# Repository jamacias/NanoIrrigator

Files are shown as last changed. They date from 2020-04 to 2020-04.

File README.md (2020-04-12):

# NanoIrrigator
A small Arduino Nano PCB shield for controlling solenoid valves for irrigation systems.

The current design is for a single channel, but may be expanded to more channels if there exists more space.

## Main features
* Single-sided PCB for CNC milling.
* 24VAC solenoid valve control with TRIAC and opto-isolator.
* Snubber circuit.

## Pics
<p align="center">
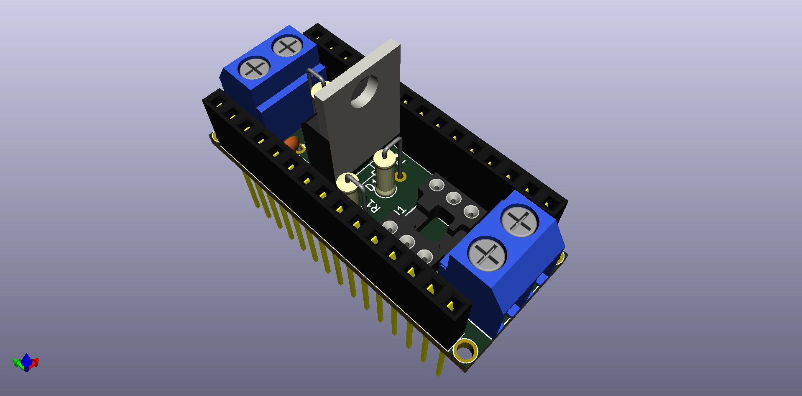
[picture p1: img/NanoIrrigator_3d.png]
    
</p>
<p align="center">
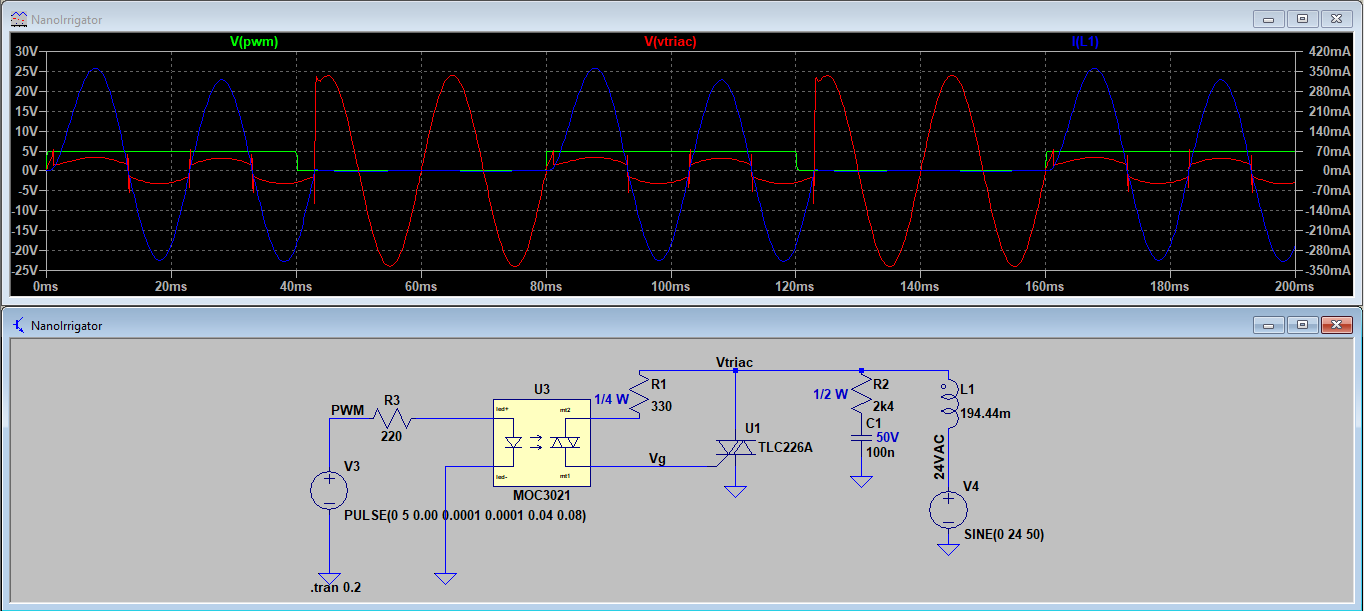
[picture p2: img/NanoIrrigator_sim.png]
    
</p>
<p align="center">
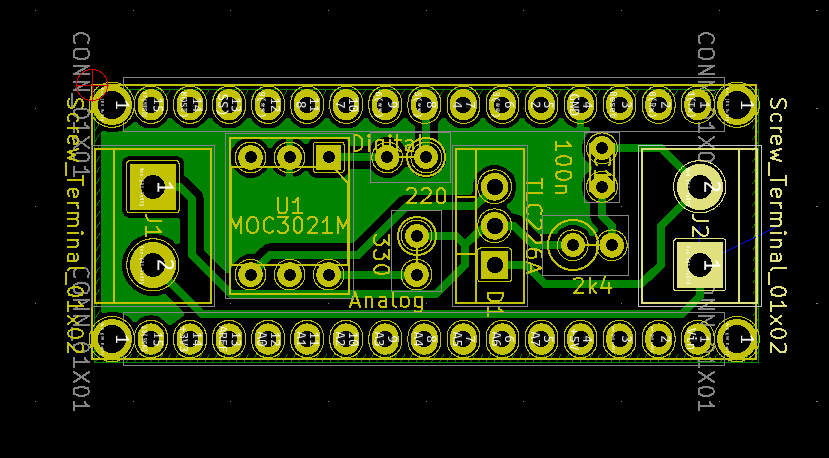
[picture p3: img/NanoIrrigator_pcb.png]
    
</p>

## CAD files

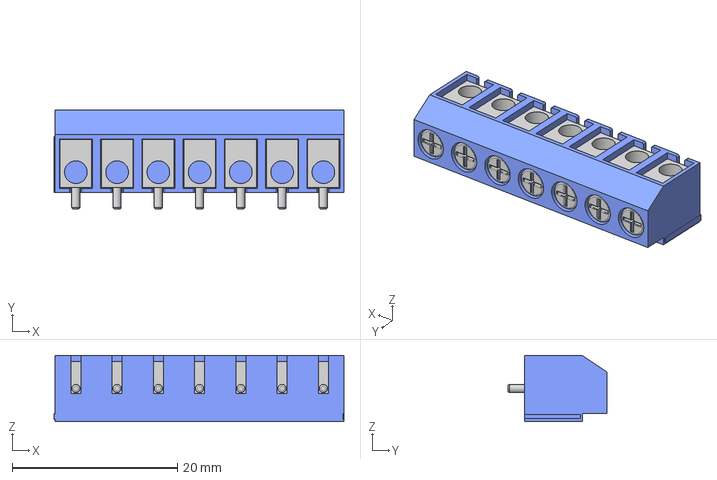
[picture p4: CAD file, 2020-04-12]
NanoIrrigator/3d_models/screw-terminal-block-5mm-2.snapshot.17/Screw Terminal Block 5mm Blue 7-way.step
35.1 x 12.0 x 8.00 mm

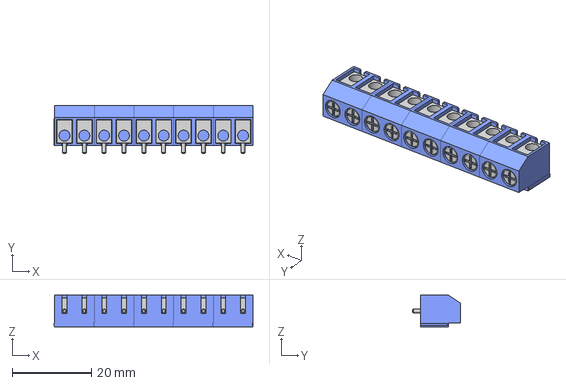
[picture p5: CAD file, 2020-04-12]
NanoIrrigator/3d_models/screw-terminal-block-5mm-2.snapshot.17/Screw Terminal Block 5mm Blue 10-way.stp
50.1 x 12.0 x 8.00 mm
Screw Terminal Block 5mm Blue 2-way x 5

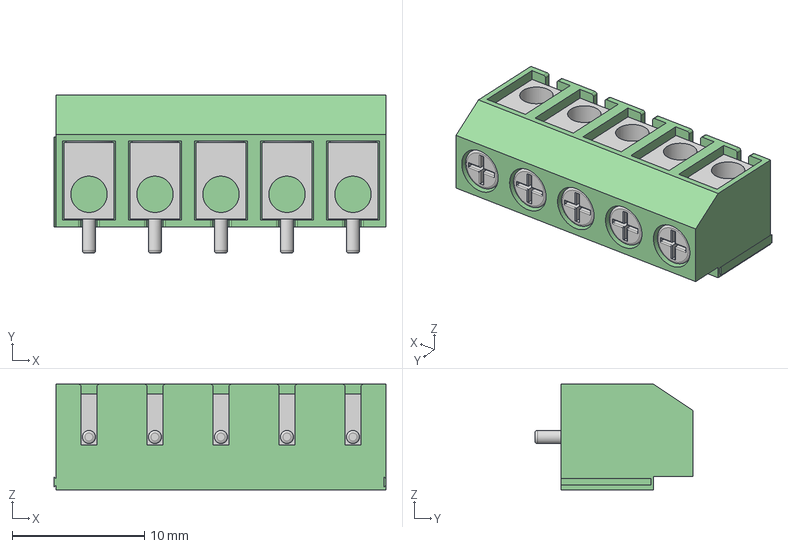
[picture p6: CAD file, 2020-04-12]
NanoIrrigator/3d_models/screw-terminal-block-5mm-2.snapshot.17/Screw Terminal Block 5mm 5-way.step
25.1 x 12.0 x 8.00 mm

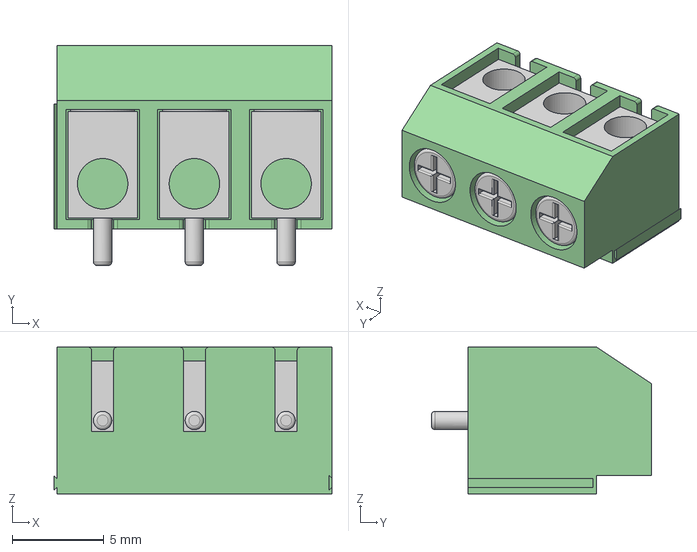
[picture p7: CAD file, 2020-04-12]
NanoIrrigator/3d_models/screw-terminal-block-5mm-2.snapshot.17/Screw Terminal Block 5mm 3-way.step
15.2 x 12.0 x 8.00 mm

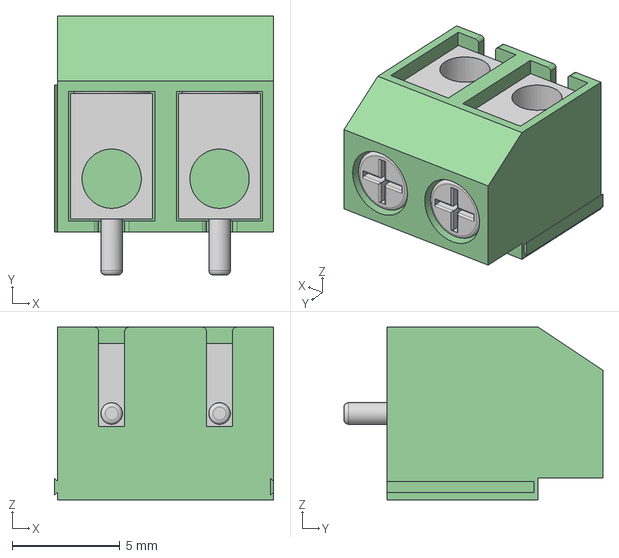
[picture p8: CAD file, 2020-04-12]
NanoIrrigator/3d_models/screw-terminal-block-5mm-2.snapshot.17/Screw Terminal Block 5mm 2-way.step
10.2 x 12.0 x 8.00 mm

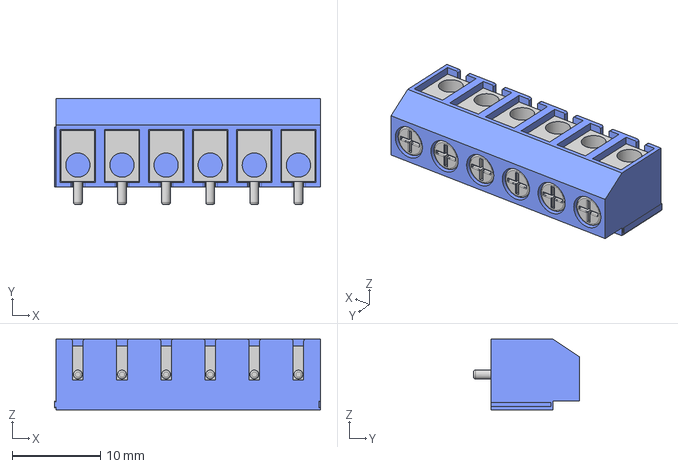
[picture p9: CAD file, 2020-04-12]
NanoIrrigator/3d_models/screw-terminal-block-5mm-2.snapshot.17/Screw Terminal Block 5mm Blue 6-way.step
30.1 x 12.0 x 8.00 mm

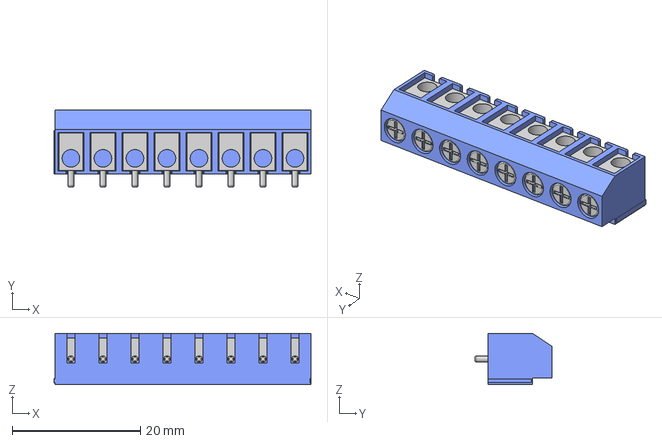
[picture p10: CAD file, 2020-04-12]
NanoIrrigator/3d_models/screw-terminal-block-5mm-2.snapshot.17/Screw Terminal Block 5mm Blue 8-way.step
40.1 x 12.0 x 8.00 mm

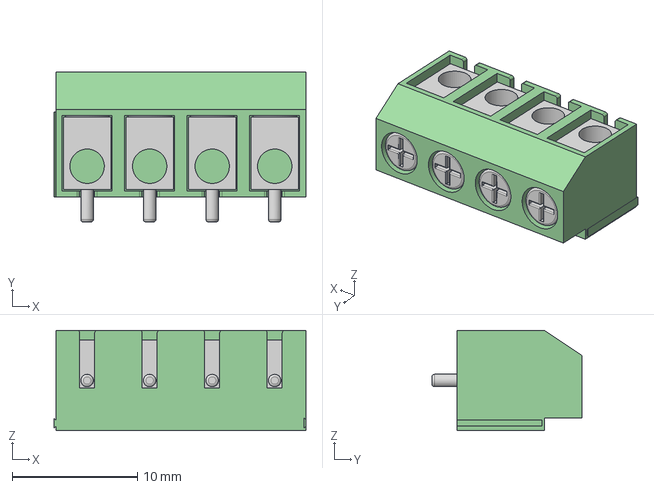
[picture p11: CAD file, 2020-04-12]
NanoIrrigator/3d_models/screw-terminal-block-5mm-2.snapshot.17/Screw Terminal Block 5mm 4-way.step
20.1 x 12.0 x 8.00 mm

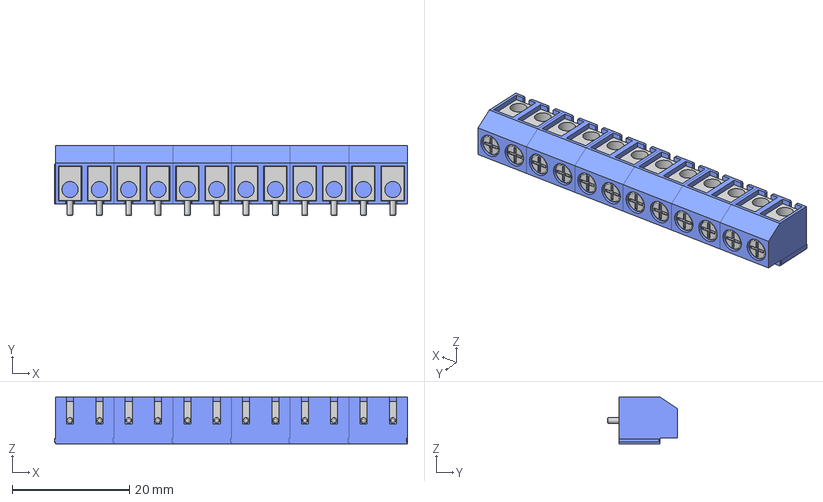
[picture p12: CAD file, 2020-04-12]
NanoIrrigator/3d_models/screw-terminal-block-5mm-2.snapshot.17/Screw Terminal Block 5mm Blue 12-way.stp
60.1 x 12.0 x 8.00 mm
Screw Terminal Block 5mm Blue 2-way x 6

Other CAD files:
NanoIrrigator/3d_models/screw-terminal-block-5mm-2.snapshot.17/Screw Terminal Block 5mm Blue 3-way.step
NanoIrrigator/3d_models/screw-terminal-block-5mm-2.snapshot.17/Screw Terminal Block 5mm Blue 5-way.step
NanoIrrigator/3d_models/screw-terminal-block-5mm-2.snapshot.17/Screw Terminal Block 5mm 8-way.step
NanoIrrigator/3d_models/screw-terminal-block-5mm-2.snapshot.17/Screw Terminal Block 5mm 6-way.step
NanoIrrigator/3d_models/screw-terminal-block-5mm-2.snapshot.17/Screw Terminal Block 5mm 7-way.step
NanoIrrigator/3d_models/screw-terminal-block-5mm-2.snapshot.17/Screw Terminal Block 5mm Blue 4-way.step
NanoIrrigator/3d_models/screw-terminal-block-5mm-2.snapshot.17/Screw Terminal Block 5mm Blue 2-way.step

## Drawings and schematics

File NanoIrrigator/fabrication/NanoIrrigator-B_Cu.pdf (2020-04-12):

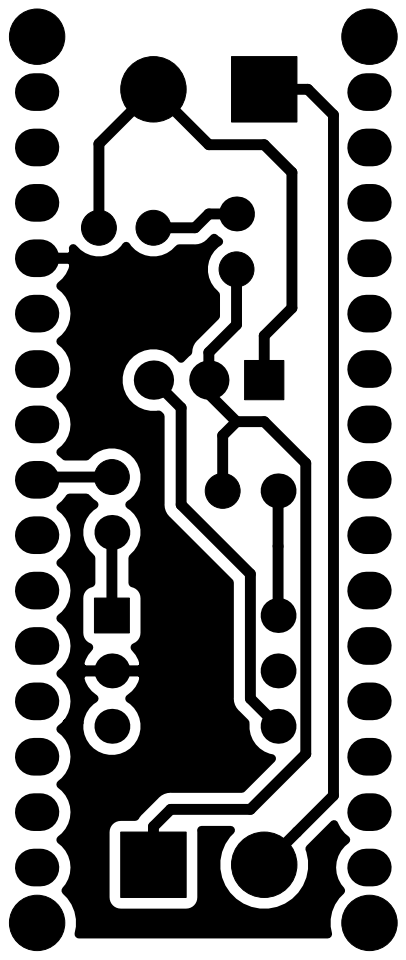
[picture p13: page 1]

File: NanoIrrigator.kicad_pcb Sheet: Author: Javier Macías Solá

Id: 1/1 Title: NanoIrrigator PCB

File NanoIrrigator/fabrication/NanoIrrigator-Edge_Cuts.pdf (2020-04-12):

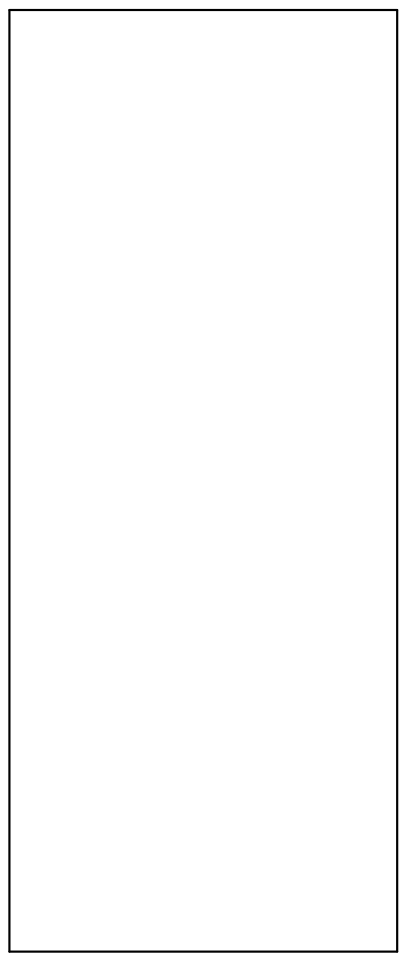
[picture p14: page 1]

File: NanoIrrigator.kicad_pcb Sheet: Author: Javier Macías Solá

Id: 1/1 Title: NanoIrrigator PCB

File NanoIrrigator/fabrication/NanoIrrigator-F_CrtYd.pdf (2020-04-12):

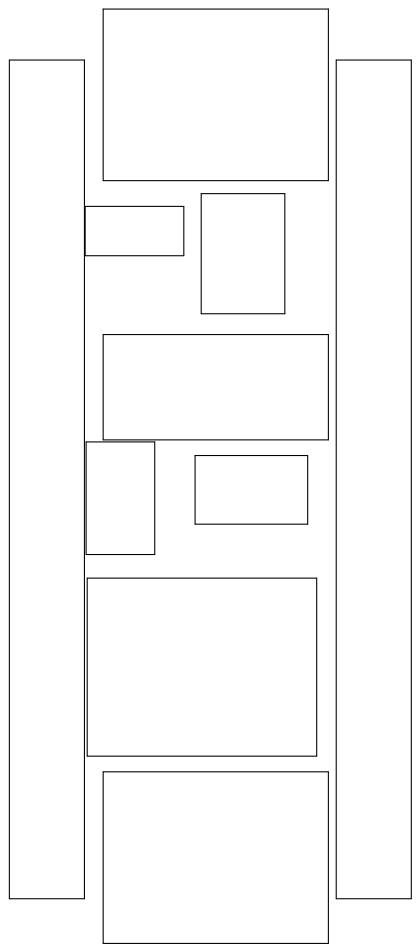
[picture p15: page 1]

File: NanoIrrigator.kicad_pcb Sheet: Author: Javier Macías Solá

Id: 1/1 Title: NanoIrrigator PCB

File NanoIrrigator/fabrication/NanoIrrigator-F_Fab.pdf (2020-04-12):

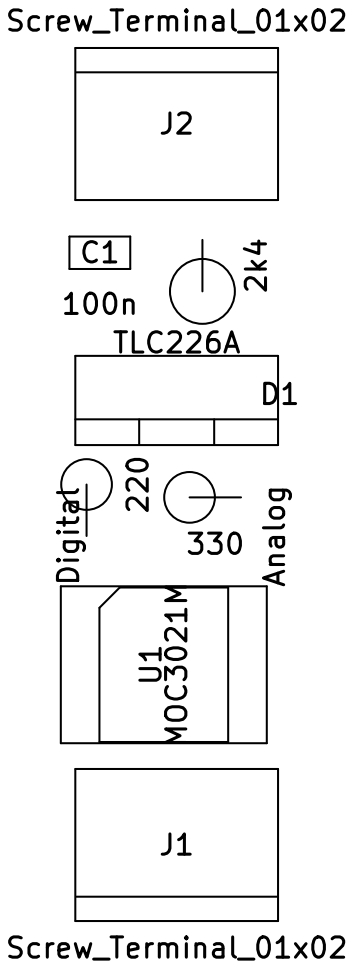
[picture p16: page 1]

File: NanoIrrigator.kicad_pcb Sheet: Author: Javier Macías Solá

Id: 1/1 Title: NanoIrrigator PCB

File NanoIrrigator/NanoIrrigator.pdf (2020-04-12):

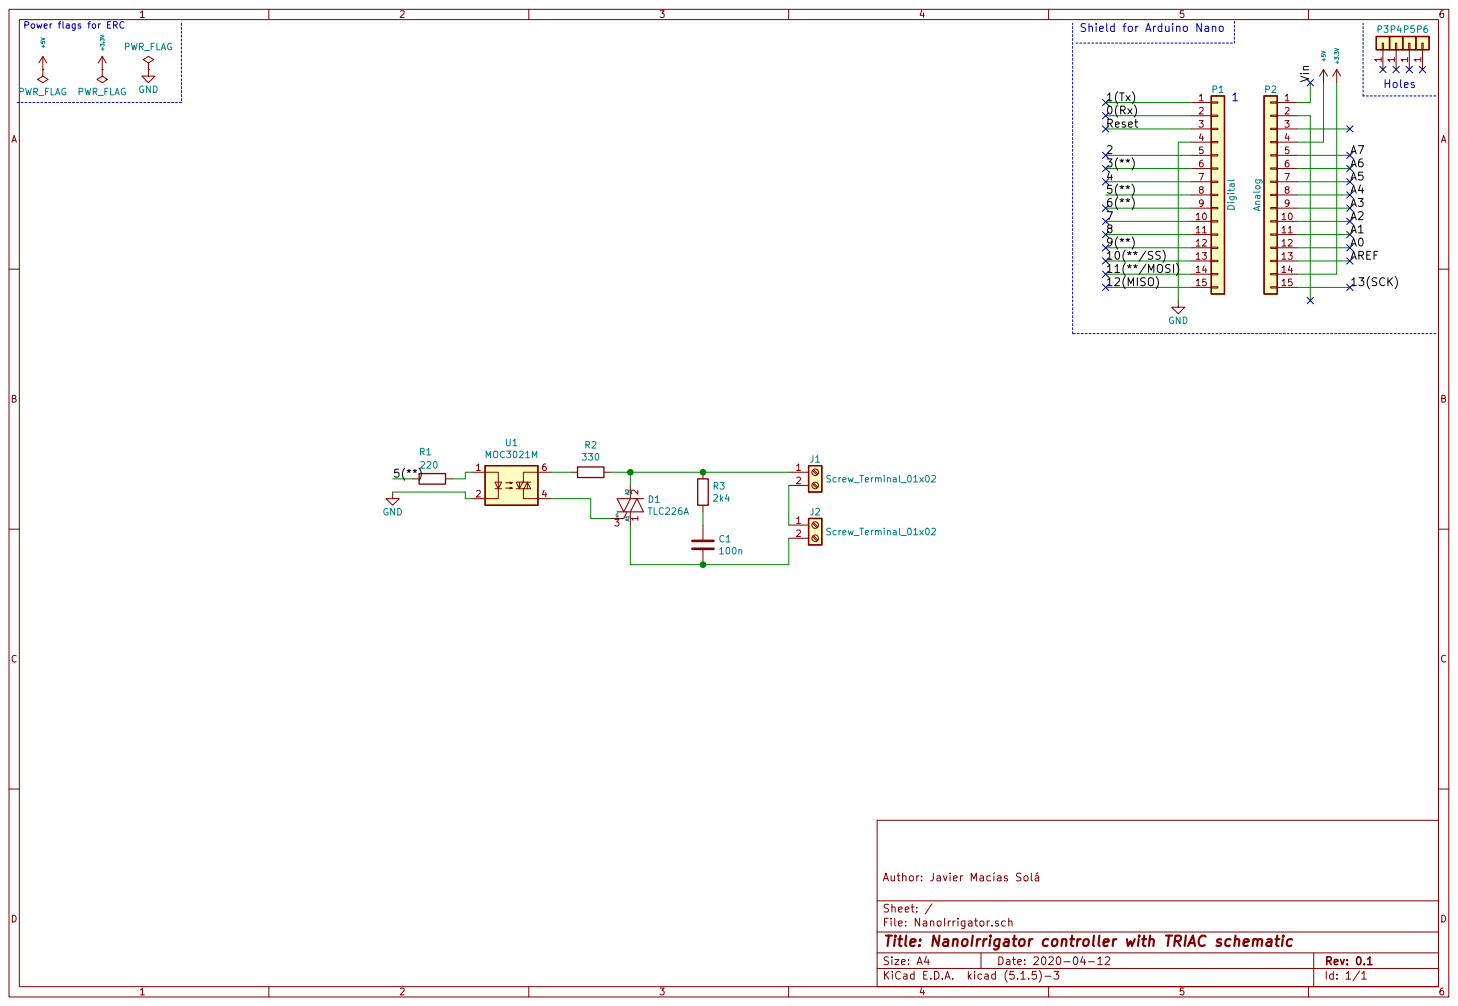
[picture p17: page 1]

Power flags for ERC
GND GND +3.3V +5V PWR_FLAG PWR_FLAG

File: NanoIrrigator.sch Sheet: / Author: Javier Macías Solá A11 A22

Id: 1/1 Title: NanoIrrigator controller with TRIAC schematic

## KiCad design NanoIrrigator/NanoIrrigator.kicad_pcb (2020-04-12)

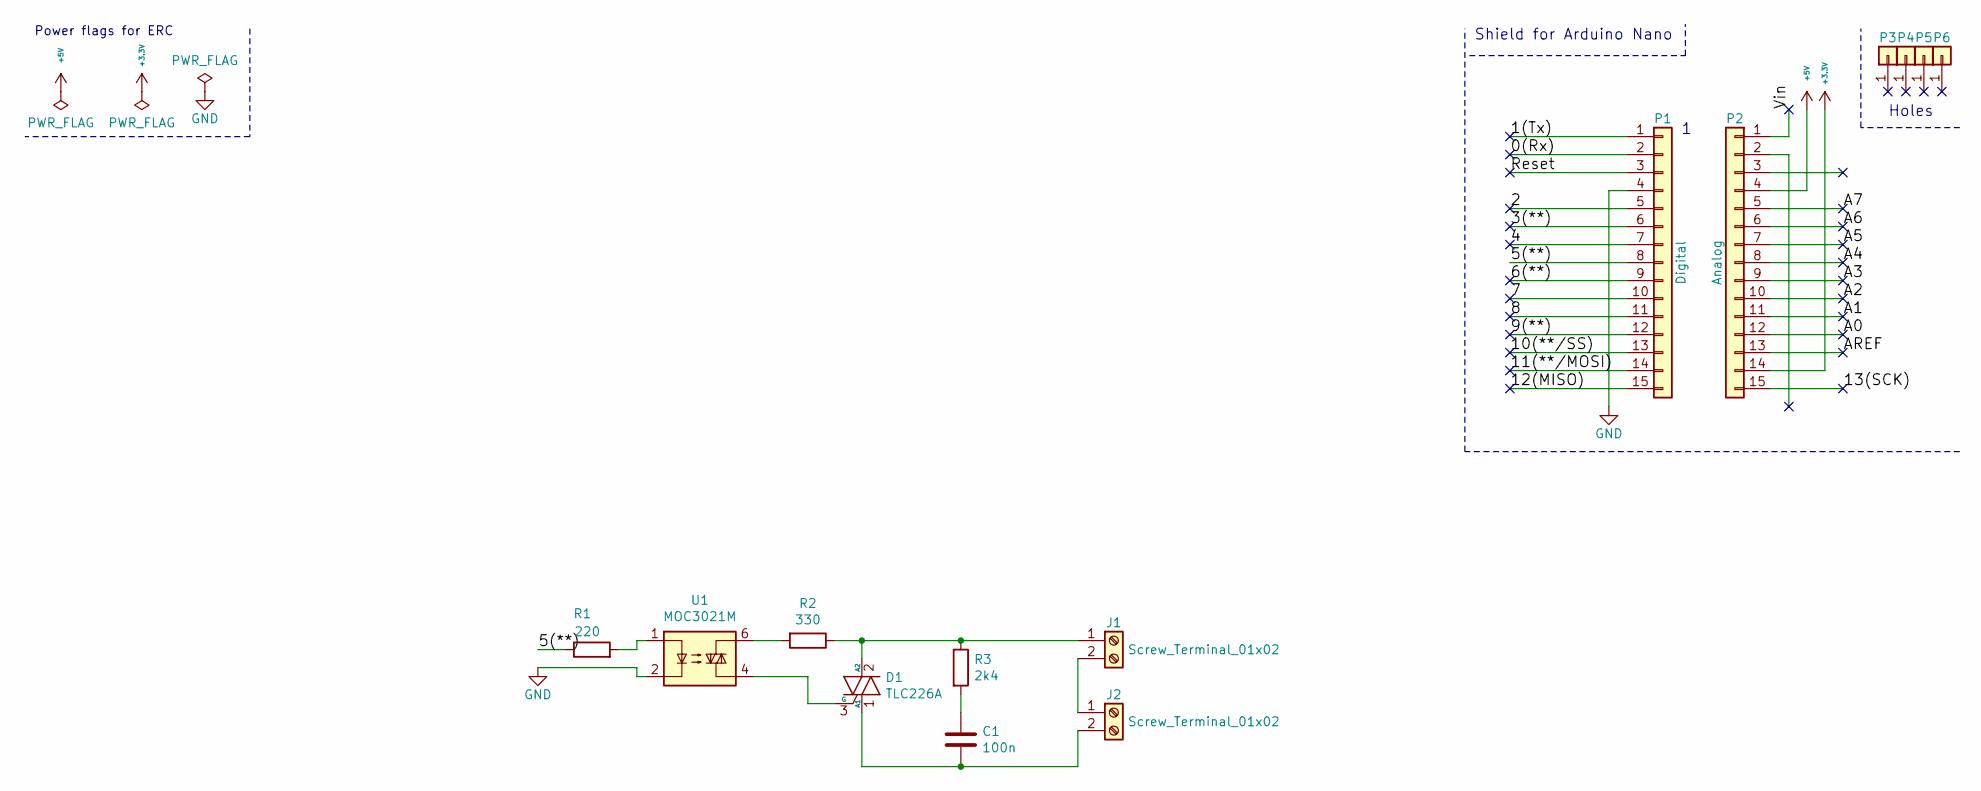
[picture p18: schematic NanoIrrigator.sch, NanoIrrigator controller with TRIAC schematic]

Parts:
C1: 100n; C_Disc_D3.0mm_W1.6mm_P2.50mm
D1: TLC226A; TO-220-3_Vertical
J1, J2: Screw_Terminal_01x02; TerminalBlock_bornier-2_P5.08mm
P1: Digital; Socket_Strip_Arduino_1x15
P2: Analog; Socket_Strip_Arduino_1x15
P3, P4, P5, P6: CONN_01X01; 1pin_Nano
R1: 220; R_Axial_DIN0207_L6.3mm_D2.5mm_P2.54mm_Vertical
R2: 330; R_Axial_DIN0207_L6.3mm_D2.5mm_P2.54mm_Vertical
R3: 2k4; R_Axial_DIN0309_L9.0mm_D3.2mm_P2.54mm_Vertical
U1: MOC3021M; DIP-6_W7.62mm_Socket

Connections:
+3V3: P2.14
+5V: P2.4
/0(Rx): P1.2
/1(Tx): P1.1
/2: P1.5
/3(**): P1.6
/4: P1.7
/5(**): P1.8, R1.1
/6(**): P1.9
/7: P1.10
/8: P1.11
/9(**): P1.12
/10(**/SS): P1.13
/11(**/MOSI): P1.14
/12(MISO): P1.15
/13(SCK): P2.15
/A0: P2.12
/A1: P2.11
/A2: P2.10
/A3: P2.9
/A4: P2.8
/A5: P2.7
/A6: P2.6
/A7: P2.5
/AREF: P2.13
/Reset: P1.3
/Vin: P2.1
GND: P1.4, U1.2
unnamed: C1.1, R3.2
unnamed: C1.2, D1.1 (A1), J2.2
unnamed: D1.2 (A2), J1.1, R2.1, R3.1
unnamed: D1.3 (G), U1.4
unnamed: J1.2, J2.1
unnamed: R1.2, U1.1
unnamed: R2.2, U1.6

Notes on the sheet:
Holes
Shield for Arduino Nano
Power flags for ERC

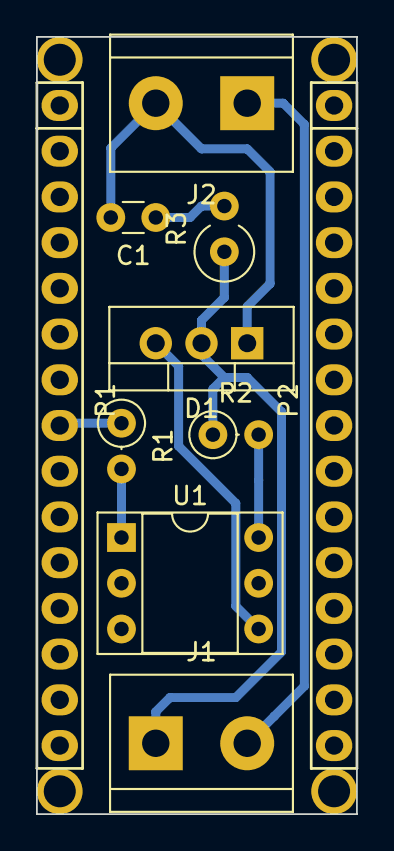
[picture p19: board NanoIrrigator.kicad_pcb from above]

Board: 2 copper layers, 17.8 x 43.2 mm, 14 parts (0 on the bottom side), 9 nets.
